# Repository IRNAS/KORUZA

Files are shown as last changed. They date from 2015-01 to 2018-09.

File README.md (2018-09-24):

Wireless optical system KORUZA
======

In this repository you can find documentation with all the plans for mechanical and electronic KORUZA parts.

Check  repository [koruza-instructions](https://github.com/IRNAS/KORUZA-instructions) if you are looking for documentation on how to assemble and use Koruza system. See [project website](http://koruza.net/) for complete specification and introduction.

Should you need any support with KORUZA system, get in touch with Institute IRNAS team. Please note that this version of the system is no longer actively supported.

---

## Licensing

We strive to make KORUZA as usefully open-source as possible.
Hardware including documentation is licensed under [CERN OHL v.1.2. license](http://www.ohwr.org/licenses/cern-ohl/v1.2)

Firmware and software originating from the project is licensed under [GNU GENERAL PUBLIC LICENSE v3](http://www.gnu.org/licenses/gpl-3.0.en.html).

Open data generated by our projects is licensed under [CC0](https://creativecommons.org/publicdomain/zero/1.0/legalcode).

All our websites and additional documentation are licensed under [Creative Commons Attribution-ShareAlike 4 .0 Unported License] (https://creativecommons.org/licenses/by-sa/4.0/legalcode).

What this means is that you can use hardware, firmware, software and documentation without paying a royalty and knowing that you'll be able to use your version forever. You are also free to make changes but if you share these changes then you have to do so on the same conditions that you enjoy.

Koruza, GoodEnoughCNC and IRNAS are all names and marks of Institut IRNAS Rače. 
You may use these names and terms only to attribute the appropriate entity as required by the Open Licences referred to above. You may not use them in any other way and in particular you may not use them to imply endorsement or authorization of any hardware that you design, make or sell.

### Contributing
By contributing to KORUZA repository you agree with the specified license and terms of use. Note significant changes in CHANGE.txt, using github comments for commits and smaller changes. 

### Manufacturing
You are required to distribute the license along with the documentation or modified documentation along with every manufactured unit. We ask you to report at monthly intervals in writing about the units you have manufactured as specified in PRODUCT.txt .

## Copyright

Copyright Institute IRNAS Rače 2016. 

This documentation describes Open Hardware and is licensed under the CERN OHL v. 1.2.
You may redistribute and modify this documentation under the terms of the [CERN OHL v.1.2.](http://ohwr.org/cernohl). This documentation is distributed WITHOUT ANY EXPRESS OR IMPLIED  WARRANTY, INCLUDING OF MERCHANTABILITY, SATISFACTORY QUALITY AND FITNESS FOR A PARTICULAR PURPOSE. Please see the CERN  OHL  v.1.2 for applicable conditions.

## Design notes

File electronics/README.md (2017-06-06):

# KORUZA control electronics

KORUZA wireless optical system is controlled through a network interface. It is based on Raspberry Pi 2B microcomputer expanded with circuit boards designed for this purpose.

The boards have been designed in Altium Designer, all sources and gerber files are available.

## KORUZA RPi shield
This board attaches directly onto the Raspberry Pi and is the input/output interface to control motors, sensors and SFP modules.

## KORUZA power module
This board accepts DC power in 12-30V (24V optimal) range and creates two regulated outputs at 5V and 9V, used for powering the Raspberry Pi and motors respectively. It attaches directly to the RPi shield or can be connected with a flat cable.

## KORUZA SFP extension plug
This board is a fake SFP module that can be plugged in an media converted and bring out the data signals. They are connected to a SATA connector as it is a high-speed differential cable commonly available.

## KORUZA SFP extension socket
This board accepts an SFP module and connects to the plug with SATA and IDC cables and to the RPi shield with an IDC cable, allowing for the remote monitoring of SFP module digital monitoring features.

# Ordering
You can order the PCBs from DirtyPCB service by following the two links or pre-panelized designs. To build KORUZA units you need two PCB panels of different thicknesses, [panel 1.0mm](http://dirtypcbs.com/view.php?share=15209&accesskey=d26ee0985b1c8a857d2a581abbbace13) and [panel 1.6mm](http://dirtypcbs.com/view.php?share=15210&accesskey=55f58673fd12db957a8ae663c1b3f456) you can order from the links provided.

---

The documentation for universal controller for unipolar stepper motors with encoders and end switches is in the repository [UniversalUnipolarStepperController](https://github.com/IRNAS/UniversalUnipolarStepperController).

Check  repository [koruza-instructions](https://github.com/IRNAS/KORUZA-instructions) if you are looking for documentation on how to assemble and use Koruza system. See [project website](http://koruza.net/) for complete specification and introduction.

Should you need any support with KORUZA system, get in touch with Institute IRNAS team and others involved in the project via [chat](https://chat.irnas.eu/).

---

#### License

All our projects are as usefully open-source as possible.

Hardware including documentation is licensed under [CERN OHL v.1.2. license](http://www.ohwr.org/licenses/cern-ohl/v1.2)

Firmware and software originating from the project is licensed under [GNU GENERAL PUBLIC LICENSE v3](http://www.gnu.org/licenses/gpl-3.0.en.html).

Open data generated by our projects is licensed under [CC0](https://creativecommons.org/publicdomain/zero/1.0/legalcode).

All our websites and additional documentation are licensed under [Creative Commons Attribution-ShareAlike 4 .0 Unported License] (https://creativecommons.org/licenses/by-sa/4.0/legalcode).

What this means is that you can use hardware, firmware, software and documentation without paying a royalty and knowing that you'll be able to use your version forever. You are also free to make changes but if you share these changes then you have to do so on the same conditions that you enjoy.

Koruza, GoodEnoughCNC and IRNAS are all names and marks of Institut IRNAS Rače. 
You may use these names and terms only to attribute the appropriate entity as required by the Open Licences referred to above. You may not use them in any other way and in particular you may not use them to imply endorsement or authorization of any hardware that you design, make or sell.

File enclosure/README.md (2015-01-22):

KORUZA enclosure
======================
The outer KORUZA enclosure houses the main 3D printed assembly and protects the device from weather as well as interfaces the mounting mechanism.

### Design overview
The enclosure is designed to be made from standard square aluminium tubing with 100mm x 100mm x 2mm dimension (outer dimensions and wall thickness) that is available from a range of suppliers. The front section features an overhang to protect the lens from direct exposure to snow and rain. 4 mounting holes on the front side on two sides serve as mounting points for the internal assembly, 4 holes on the top towards the rear for the mounting mechanism and two holes on the rear for mounting the back cover. The large hole on the bottom side is for mounting the PG16 euroflex tube connector.

### Manufacturing
The enclosure can be manufactured with the following methods:
* 3 axis CNC: Manually rotate the tube and cute each side separately. Suitable for low volume
* 4 axis CNC: Automatically cut the tube on all sides. Suitable for low volume.
* Tube laser cutter: Automatically cut all sides. Suitable for high volumes.

KORUZA enclosure

### Lid / cover
The back cover for the enclosure is 3D printed and made to house electonics. Designed in OpenSCAD and using [IRNAS OpenSCAD-Lib](https://github.com/IRNAS/OpenSCAD-lib) for common mechanical elements. 3D print from ABS, attach to enclosure with M3 screws.

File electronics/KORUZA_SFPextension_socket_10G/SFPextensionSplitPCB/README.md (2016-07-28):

# SFP extension Split

### ISSUE
* add via tenting on output (gerber) files - DONE

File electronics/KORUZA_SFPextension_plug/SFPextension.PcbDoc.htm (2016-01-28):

Reporting Options

# File in Previous Format

Date | : | 2/10/2014
Time | : | 2:40:51 PM
Filename | : | Z:\Projects\AltiumProjects\SFPextension.PcbDoc

Version | Warning
Altium Designer update 19 | CAUTION - Air Gap Width attribute was introduced to Polygon Connect Style Rule. Air Gap Width attribute now controls the distance between poured polygon and pads on the same net - this value was previosuly taken from clearance rule while ignoring net subscope leading to sometime unexpected results.
Release 13 | CAUTION - Silkscreen Over Component Pads Rules are converted to Silk To Solder Mask Clearance Rules. Suggest examining rule scopes for accuracy.
Release 14 | CAUTION - The Differential Pairs Routing rule added support for control of the width. Be aware that Width rules pertaining to differential pairs need to be manually moved to the Differential Pairs Routing rule.

This file was generated by an earlier version of the software

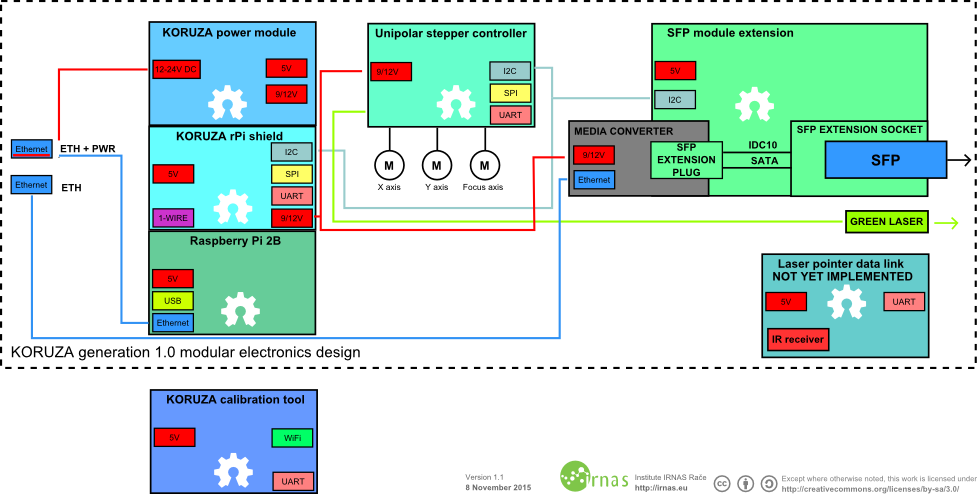
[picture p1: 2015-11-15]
diagrams/ElectronicsDiagram.png

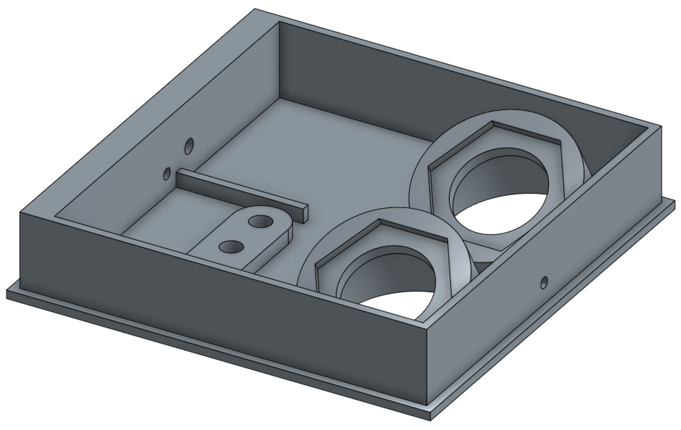
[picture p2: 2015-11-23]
enclosure/enclosure_cover.png

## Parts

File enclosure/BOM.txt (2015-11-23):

1 enota:

1x square tube 100x100x2 x 475mm
1x L profile 100x100x5 x 250mm
1x U profile 100x35x5 x 160mm
1x pritrditev za na štango z vsemi vijaki

1x bolt_eye_DIN444A_M10x45
2x nut_thin_ISO4035_M10

1x bolt_round_head_square_neck_DIN603_M10x70
1x washer_spring_lock_DIN127_M10
3x nut_thin_ISO4035_M10

1x bolt_HEX_ISO4017_DIN933_M10x160
1x washer_spring_lock_DIN127_M10
7x nut_thin_ISO4035_M10

2x screw_M4
2x washer_spring_lock_DIN127_M4
2x nut_DIN934_M4

+ spring washer m10 in m4
+ šrauf m4
+ assembly

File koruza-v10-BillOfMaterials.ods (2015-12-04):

KORUZA generation 1.0 – Bill of materials
Institute IRNAS Rače – Licensed under CERN OHL – 2.12.2015
Preliminary information, not for ordering or general use, you have been warned!
Module | Sub-module | Part name | Description | Quantity | Part nr.
Electronics |  | Power module | Circuit board from 24V in to 5V and 9V out | 1 | E-1
Electronics |  | Raspberry pi shield | Shield for interfacing Rpi with KORUZA electronics | 1 | E-2
Electronics |  | Sfp extension plug | Module for interfacing Media converter | 1 | E-3
Electronics |  | Sfp extension socket | Module for interfacing SFP module | 1 | E-4
Electronics |  | Universal unipolar stepper driver | Module for controlling stepper motors and green laser | 1 | E-5
Electronics |  | Raspberry Pi 2B microcomputer | Brains of the system | 1 | E-6
Electronics |  | PoE injector 24V | Passive PoE injector | 1 | E-7
Electronics |  | SFP module 40km+ BiDi SC with DDM | Electro-optical transceiver | 1 | E-8
Electronics |  | Green laser 5mV, 3.3V |  | 1 | E-9
Electronics |  | Motor 24BYJ48 |  | 3 | E-10
Electronics |  | Waterproof eth connector |  | 1 | E-11
Electronics |  | Waterproof eth + pwr connectors |  | 1 | E-12
Electronics |  | TP-Link MC220L media converter |  | 1 | E-13
Electronics |  | Cable IDC long | IDC10 35cm | 1 | E-14
Electronics |  | Cable IDC short | IDC10 10cm | 1 | E-15
Electronics |  | SATA cable | 10cm long, straight straing | 1 | E-16
Electronics |  | Micromatch cable | 25cm | 1 | E-17
Electronics |  | Cable power 0.75mm^2 red-black | 20cm | 1 | E-18
Electronics |  | Cable power jack 2.1mm | 25cm | 1 | E-19
Electronics |  | Micro SD card, 8GB |  | 1 | E-20
Mechanical | Fasteners | Set screw HEX socket DIN913 M3x16 |  | 1 | M-F1
Mechanical | Fasteners | Screw HEX socket DIN912 M3x25 |  | 9 | M-F3
Mechanical | Fasteners | Screw HEX socket DIN912 M3x35 |  | 18 | M-F4
Mechanical | Fasteners | Screw HEX socket DIN912 M4x45 |  | 4 | M-F5
Mechanical | Fasteners | Screw TORX BN6404 M3x10 |  | 17 | M-F6
Mechanical | Fasteners | Screw HEX socket DIN912 M4x12 |  | 12 | M-F7
Mechanical | Fasteners | Screw HEX socket DIN912 M4x70 |  | 2 | M-F8
Mechanical | Fasteners | Screw HEX DIN933 M5x80 | 70mm to 80mm length works equally well | 1 | M-F9
Mechanical | Fasteners | Threaded rod M5x65 |  | 2 | M-F10
Mechanical | Fasteners | Nut, square DIN562 M3 |  | 42 | M-F11
Mechanical | Fasteners | Nut, square DIN562 M4 |  | 22 | M-F12
Mechanical | Fasteners | Long nut, HEX DIN6334 M5 |  | 3 | M-F13
Mechanical | Fasteners | Washer M3 DIN921 |  | 3 | M-F14
Mechanical | Fasteners | Washer M4 DIN921 |  | 7 | M-F15
Mechanical | Fasteners | Thin nut ISO4035 M10 |  | 10 | M-F16
Mechanical | Fasteners | Eye bolt Screw DIN444A M10x40 |  | 1 | M-F17
Mechanical | Fasteners | Screw round head square neck bolt DIN603 M10x75 |  | 1 | M-F18
Mechanical | Fasteners | Screw HEX bolt DIN933 M10x160 |  | 1 | M-F19
Mechanical | Fasteners | Washer M10 |  | 4 | M-F20
Mechanical | Fasteners | Spring lock washer DIN127 M10 |  | 3 | M-F21
Mechanical | Fasteners | Nut, HEX, M5 DIN934 M5 |  | 1 | M-F22
Mechanical | 3D Printed | SFP module sleeve |  | 1 | M-P1
Mechanical | 3D Printed | SFP mount |  | 1 | M-P2
Mechanical | 3D Printed | Ring outer |  | 1 | M-P4
Mechanical | 3D Printed | Ring inner |  | 1 | M-P5
Mechanical | 3D Printed | Lens mount outer |  | 1 | M-P6
Mechanical | 3D Printed | Lens mount |  | 1 | M-P7
Mechanical | 3D Printed | Laser mount |  | 1 | M-P8
Mechanical | 3D Printed | Wedge left |  | 1 | M-P9
Mechanical | 3D Printed | Wedge right |  | 1 | M-P10
Mechanical | 3D Printed | MC mount |  | 1 | M-P12
Mechanical | 3D Printed | Motor mount |  | 1 | M-P13
Mechanical | 3D Printed | Inner SFP mount |  | 1 | M-P14
Mechanical | 3D Printed | Lid |  | 1 | M-P15
Mechanical | 3D Printed | bracket |  | 4 | M-P16
Mechanical | 3D Printed | Half-bracket |  | 1 | M-P17
Mechanical | 3D Printed | Pin with hole |  | 2 | M-P18
Mechanical | 3D Printed | Triangle |  | 1 | M-P19
Mechanical | Other | Rubber | 10x10cm 5mm not reinforced | 1 | M-O1
Mechanical | Other | 8mm stainless steel rod – 200mm |  | 4 | M-O2
Mechanical | Other | Lens | Plano convex 50mm FL=100mm | 1 | M-O3
Mechanical | Other | Spring 10x20x0.7mm |  | 2 | M-O4
Mechanical | Other | Sliding bushing |  | 6 | M-O6
Mechanical | Other | Cable ties 200x3.6mm |  | 2 | M-O7
Mechanical | Other | Coupler M5 |  | 3 | M-O8
Mechanical | Other | M3 male-female spacer 10mm long |  | 10 | M-O9
Mechanical | Other | Spring 49/35/4 |  | 1 | M-O10
Mechanical | Other | Bearing F624ZZ |  | 1 | M-O11
Mechanical | Other | Square profile | Custom made | 1 | M-E1
Mechanical | Enclosure | U-profile | Custom made | 1 | M-E2
Mechanical | Enclosure | L-profile | Custom made | 1 | M-E3
Mechanical | Enclosure | Mounting bracket set |  | 1 | M-E4
Tools |  | Philips screwdriver
Tools |  | Hammer
Tools |  | Combination pliers
Tools |  | tongue-and-groove pliers
Tools |  | slotted screwdriver
Tools |  | HEX key 1.5, 2.5, 3mm
Tools |  | utility knife
Tools |  | Battery drill
Tools |  | drill 3mm, 8mm, 8.1mm
Tools |  | 10mm reamer
Tools |  | TORX screwdriver T10
Tools |  | measuring tape

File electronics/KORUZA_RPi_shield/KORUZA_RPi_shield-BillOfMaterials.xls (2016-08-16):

KORUZA Raspberry PI shield Bill of Materials
Comment | Description | Designator | Footprint | LibRef | Quantity | Order | Farnell | TME
Capacitor | Capacitor MLLC 100n 5V | C1, C3, C4, C6, C7, C9 | 0603 | Capacitor | 6 |  | http://si.farnell.com/tdk/c1608x5r1h104k080aa/cap-mlcc-x5r-100nf-50v-0603/dp/2211177
Capacitor | Capacitor, Tantalum, 10uF 10% 20V MCCT-B (3528) | C2, C5, C8 | AVX-CAPC3528_V | CMP-0279-00001-1 | 3 |  | http://si.farnell.com/avx/taja106m016r/cap-tant-10uf-16v-case-a/dp/2333010
DC power connection | Screw terminal block, 2way | Conn1, Conn2, Conn3 | MKDSN 2,5/ 2-5,08 and powercon | PowerScrewTerminal | 3 |  | http://si.farnell.com/camdenboss/ctb0102-2/terminal-block-wire-to-brd-2pos/dp/2493614
LED | LED diode smd right angle white | D1, D2, D3 | 1206/0805 diode | LED | 3 |  | http://si.farnell.com/multicomp/ovs-2101/led-2-8x0-8x1-2mm-side-emitting/dp/1716775
Zener | Zener diode 15V | D4 | DIOMELF3517N | Zener | 1 |  | http://si.farnell.com/vishay-semiconductor/zmy15-gs08/diode-zener-1w-15v/dp/1617743
1A | 1A fuse PTC SMD | F1 | 1210 | Fuse | 1 |  | http://si.farnell.com/multicomp/mc36221/fuse-ptc-reset-smd-6v-1a/dp/1861192
IDC10 | IDC 10 pin male | P1, P6, P8 | IDC10 | IDC10 | 3 |  | http://si.farnell.com/amphenol/t821110a1s100ceu/header-vertical-2-54mm-10way/dp/2215304
Header for RaspberryPI | Header, 40-pin, 2 row, 2.54mm pitch | P2 | RaspberryPI_B+ | RaspberryPI 2B | 1 |  | http://si.farnell.com/harwin/m20-6112045/socket-pc-104-40way/dp/1569232
Header 3 | Header, 3-Pin | P3, P4 | HDR1X3 | Header 3 | 2 | one header 40pin breakable needed | http://si.farnell.com/te-connectivity-amp/825433-5/header-1row-5way/dp/1187826
Header 2 | Header, 2-Pin | P5, P9 | HDR1X2 | Header 2 | 2 | one header 40pin breakable needed | http://si.farnell.com/te-connectivity-amp/825433-5/header-1row-5way/dp/1187826
Header 5 | Header, 5-Pin | P7 | HDR1X5 | Header 5 | 1 | one header 40pin breakable needed | http://si.farnell.com/te-connectivity-amp/825433-5/header-1row-5way/dp/1187826
Micromatch | Micro-Match female PCB connector 10 Positions THT | PoExtension1, PoExtension2 | 8-188275-0 | 1-215079-0 | 2 |  | http://si.farnell.com/te-connectivity-amp/8-188275-0/connector-receptacle-smt-1-27mm/dp/3784745
Resistor 10k | Resistor 0805 smd | R1, R5, R7, R8, R9, R10, R11, R12, R13, R14, R19, R21, R22, R23, R25 | RESC2012X06N | Resistor | 15 |  | http://si.farnell.com/multicomp/mc0063w0603510k/res-thick-film-10k-5-0-063w-0603/dp/9331700
Resistor 0 | Resistor 0805 smd | R2, R4, R18, R20, R24 | RESC2012X06N | Resistor | 5 |  | http://si.farnell.com/multicomp/mc0063w06030r/resistor-thick-film-0r-0-063w/dp/9331662
Resistor 4k7 | Resistor 0805 smd | R3, R6 | RESC2012X06N | Resistor | 2 |  | http://si.farnell.com/multicomp/mc0063w060354k7/res-thick-film-4k7-5-0-063w-0603/dp/9332154
Resistor 1k | Resistor 0805 smd | R15, R16, R17 | RESC2012X06N | Resistor | 3 |  | http://si.farnell.com/multicomp/mc0063w060354k7/res-thick-film-4k7-5-0-063w-0603/dp/9332154
Mosfet NDT2955 | P MOSFET | T1, T2, T3 | SOT230P700X180-4N | NDT2955 | 3 |  | http://si.farnell.com/fairchild-semiconductor/ndt2955/mosfet-p-ch-60v-2-5a-sot-223/dp/9846271
Voltage regulator | LD1117S33TR | U1, U2, U3 | SOT-223_L | CMP-0244-00310-1 | 3 |  | http://si.farnell.com/texas-instruments/lm1117mp-3-3/v-reg-ldo-3-3v-1117-sot-223-3/dp/9778195
Transistor array | Darlington array ULN2003 | U4 | SO-16 narrow | ULN2003 | 1 |  | http://si.farnell.com/texas-instruments/uln2003adr/darlington-array-7npn-2003ade4/dp/1125398RL

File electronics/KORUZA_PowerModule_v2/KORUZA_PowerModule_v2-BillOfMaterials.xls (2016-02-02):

KORUZA Power module V2
Comment | Description | Designator | Footprint | LibRef | Quantity | Order | Farnell | TME
Power innput | Screw terminal or DC socket | Conn1 | MKDSN 2,5/ 2-5,08 | PowerScrewTerminal | 1 |  | http://si.farnell.com/multicomp/mj-180ph/socket-pcb-dc-power-12vdc-4a/dp/1737251
9V output | Screw terminal | Conn2 | MKDSN 2,5/ 2-5,08 | PowerScrewTerminal | 1 |  | http://si.farnell.com/camdenboss/ctb0102-2/terminal-block-wire-to-brd-2pos/dp/2493614
LED | LED diode | D1 | 1206/0805 diode | LED | 1 |  | http://si.farnell.com/rohm/sml-310vtt86l/led-smd-0603-red/dp/1685064
TVS diode | TVS bidirectional diode 36V | D2 | DIOM4750X18N | TVS diode | 1 |  | http://si.farnell.com/vishay-semiconductor/smaj36ca-e3-61/diode-tvs-400w-36v-bidir-sma/dp/1698863RL
IDC10 | IDC 10pin male | P1 | IDC10 | IDC10 | 0 | if using cable | http://si.farnell.com/amphenol/t821110a1s100ceu/header-vertical-2-54mm-10way/dp/2215304
IDC10 | IDC 10pin female | P1 | IDC10 | IDC10 | 1 | if connected to shield | http://si.farnell.com/multicomp/2214s-10sg-85/socket-pcb-2-row-vert-10way/dp/1593490
Header 2 | Header, 2-Pin | P2, P4 | HDR1X2 | Header 2 | 1 | do not install
USB | USB A standard receptacle | P3 | USB A THT | USB | 1 | do not install
1k | Resistor 0805 smd | R1 | RESC2012X06N | Resistor | 1 | do not install
LM2596 module | LM2596 module | U1, U2 | LM2596 module | LM2596 module | 2 | do not install

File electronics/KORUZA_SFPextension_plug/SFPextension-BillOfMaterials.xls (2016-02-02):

KORUZA SFP extension plug
Comment | Description | Designator | Footprint | LibRef | Quantity | Order | Farnell | TME
SATA | sata | P1 | SATA pcb | SATA | 1 |  | http://si.farnell.com/webapp/wcs/stores/servlet/ProductDisplay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
IDC10 | Header, 5-Pin, Dual row | P4 | HDR2X5_CEN | Header 5X2A | 1 |  | http://si.farnell.com/amphenol/t821110a1s100ceu/header-vertical-2-54mm-10way/dp/2215304
SFP connector |  | SFP1 | SFP pcb con | SFP connector | 0 | PCB itself

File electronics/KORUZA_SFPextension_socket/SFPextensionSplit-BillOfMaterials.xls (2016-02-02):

KORUZA SFP extension socket
Comment | Description | Designator | Footprint | LibRef | Quantity | Order | Farnell | TME
Capacitor | General capacitor | C1 | RESC2012X06N | Capacitor | 1
SATA | sata | P1 | SATA pcb | SATA | 1 |  | http://si.farnell.com/webapp/wcs/stores/servlet/ProductDisplay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
IDC10 | IDC 10pin | P2, P3 | IDC10 | IDC10 | 2 |  | http://si.farnell.com/amphenol/t821110a1s100ceu/header-vertical-2-54mm-10way/dp/2215304
SFP connector |  | SFP1 | SFP receptacle | SFP connector | 1 |  | http://si.farnell.com/te-connectivity/1888247-2/connector-sfp-rcpt-20pos-smt/dp/2399618
SFP cage |  | SFP1 | SFP cage | SFP cage | 1 |  | http://si.farnell.com/amphenol-commercial-products/u77a1118200t/cage-1-port-sfp-connector/dp/1256177

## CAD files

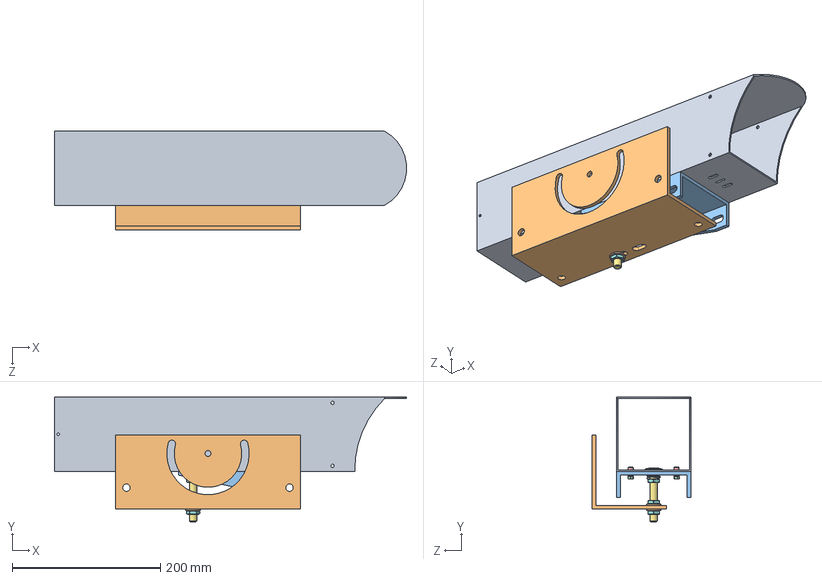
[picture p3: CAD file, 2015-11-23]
enclosure/enclosure.SLDASM
474.7 x 168.0 x 133.0 mm
square tube 100x100x2
L profile 100x100x5
U profile 100x35x5
nut_DIN934_M4 x 2
screw_HEX_SOCKET_ISO4762_DIN912_M4x12 x 2
washer_spring_lock_DIN127_M4 x 2
bolt_round_head_square_neck_DIN603_M10x70
nut_thin_ISO4035_M10 x 3
washer_spring_lock_DIN127_M10
washer_ISO7089_DIN125A_M10_10.5x20 x 2

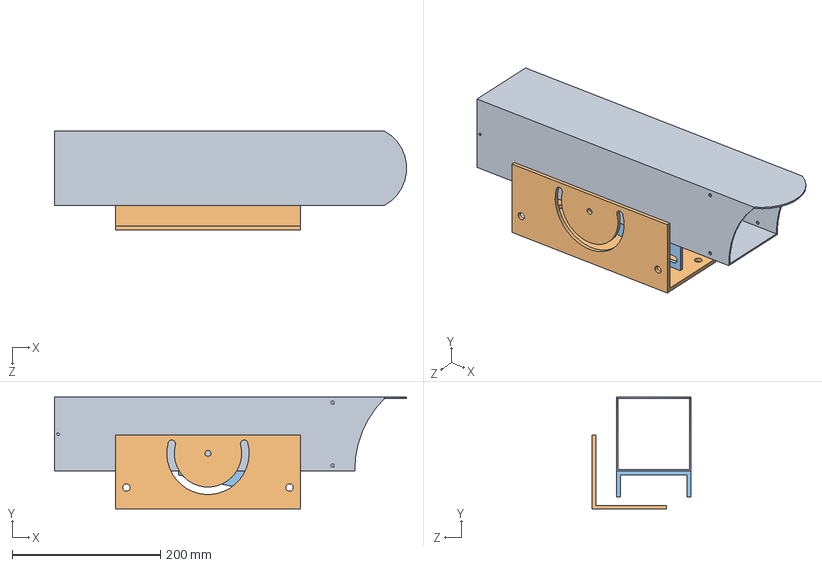
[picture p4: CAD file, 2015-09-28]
enclosure/koruza enclosure.SLDASM
474.7 x 151.0 x 133.0 mm
square tube 100x100x2
L profile 100x100x5
U profile 100x35x5

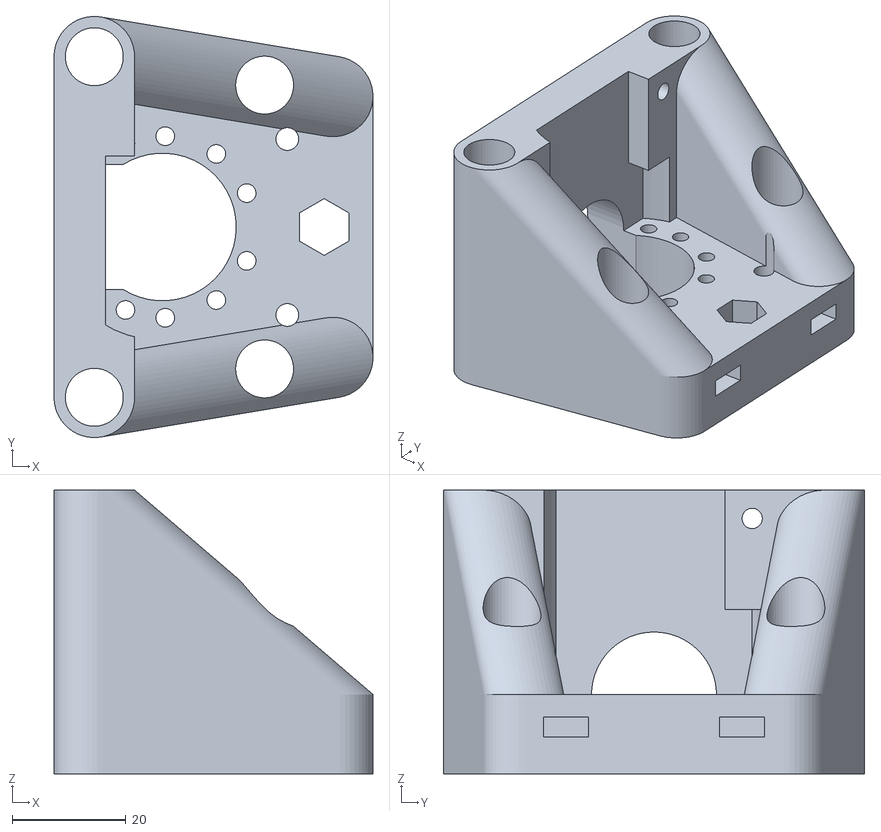
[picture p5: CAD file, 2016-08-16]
main_structure/koruza-v10-10G-sfp_mount.stl
56.2 x 74.2 x 50.0

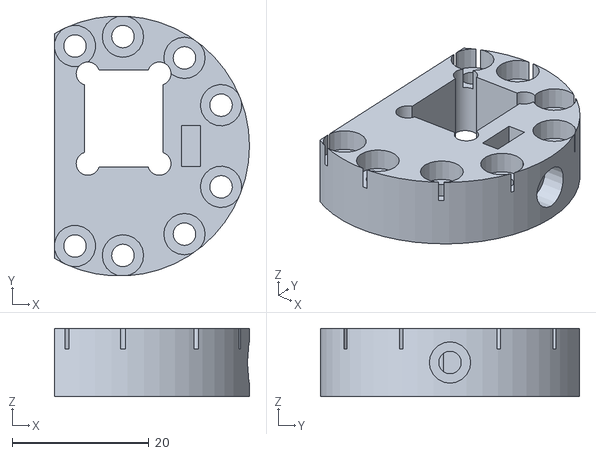
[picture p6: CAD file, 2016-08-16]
main_structure/koruza-v10-10G-sfp_mount_bracket.stl
28.5 x 37.9 x 10.0

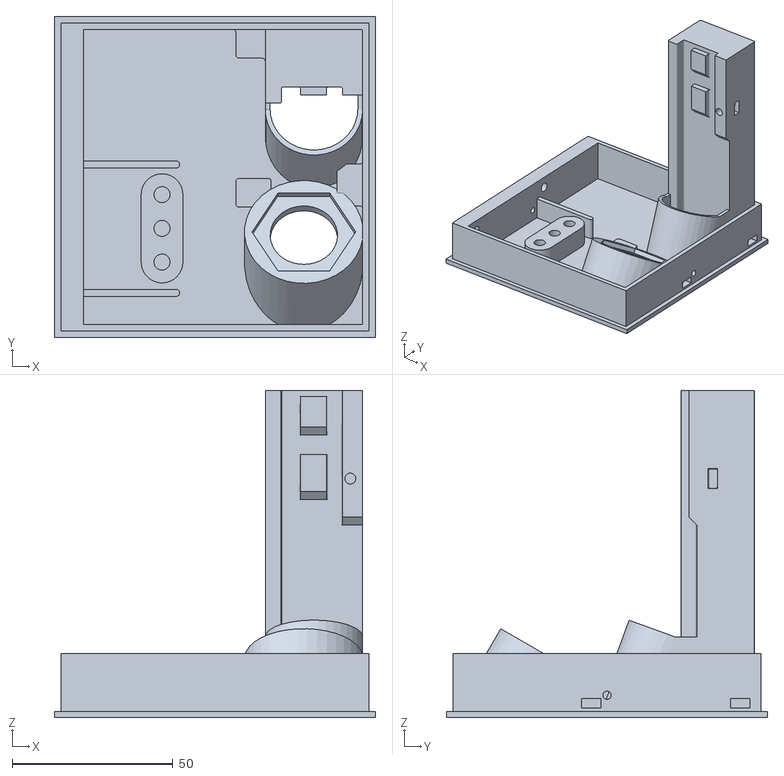
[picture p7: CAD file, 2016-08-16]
main_structure/koruza-v10-10G-enclosure-cover.stl
100.0 x 100.0 x 102.0

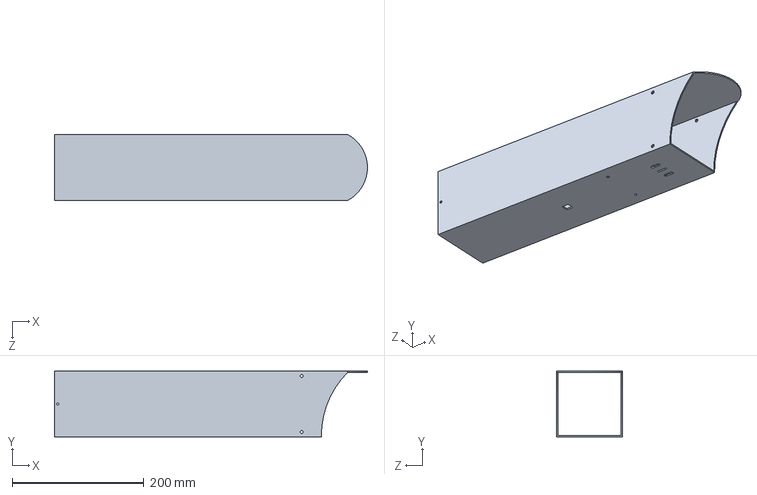
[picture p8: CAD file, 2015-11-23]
enclosure/square tube 100x100x2.STEP
475.0 x 100.0 x 100.0 mm

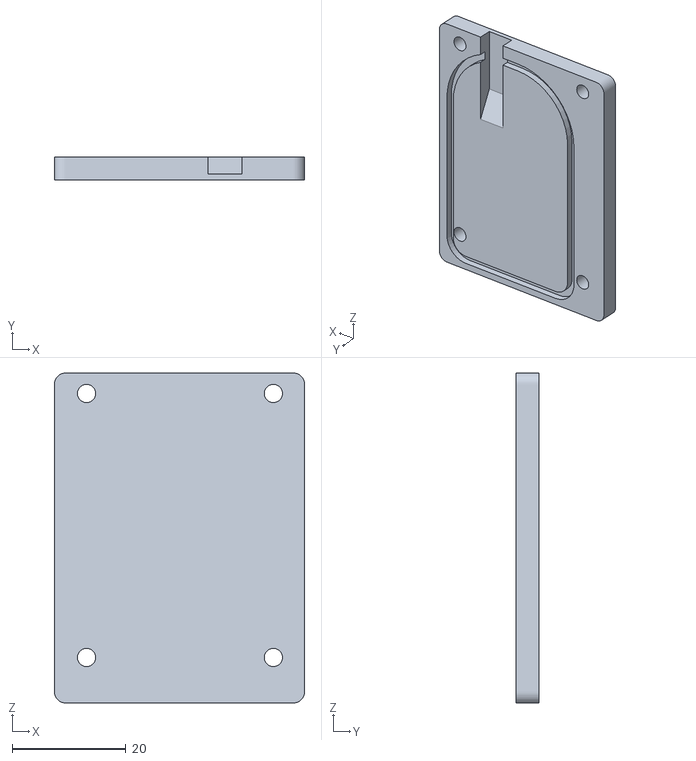
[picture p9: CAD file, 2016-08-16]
main_structure/koruza-v10-10G-enclosure-cover-lid.stl
44.0 x 4.00 x 58.0

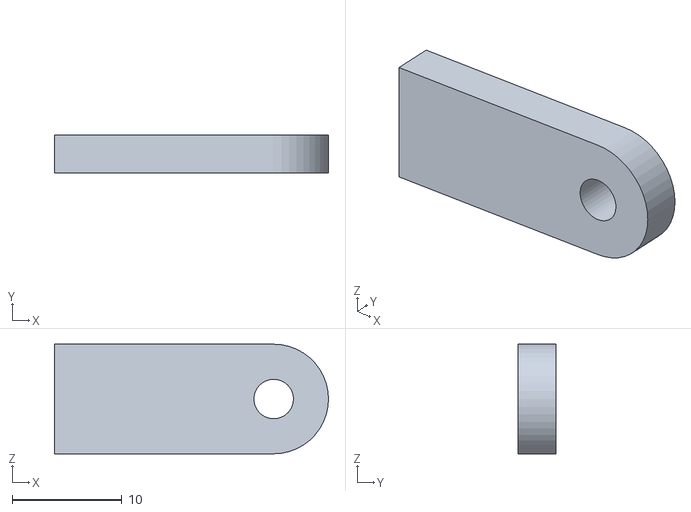
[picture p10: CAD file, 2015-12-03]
main_structure/koruza-v10-halfbracket.stl
25.0 x 3.50 x 10.0

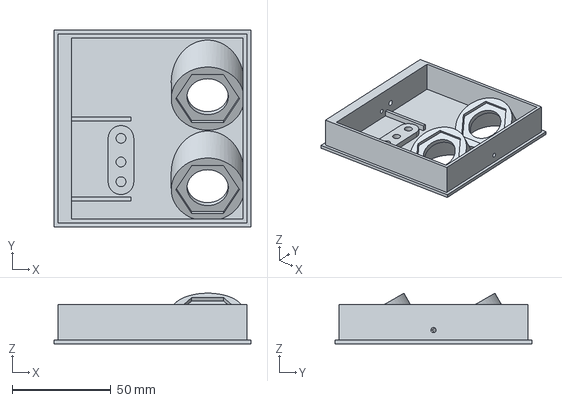
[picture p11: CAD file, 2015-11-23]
enclosure/enclosure_cover.step
100.0 x 100.0 x 25.7 mm

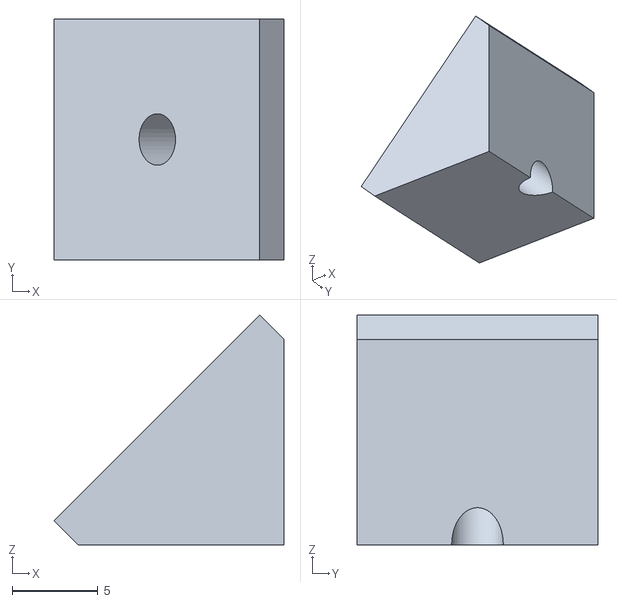
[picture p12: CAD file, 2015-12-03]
main_structure/koruza-v10-triangle.stl
13.4 x 14.0 x 13.4

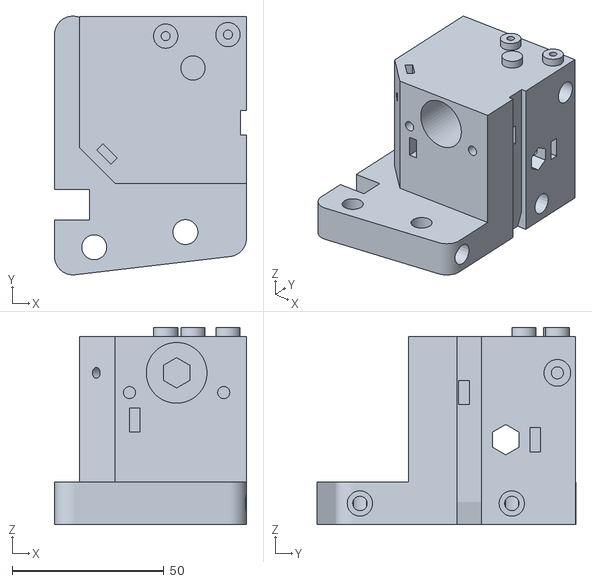
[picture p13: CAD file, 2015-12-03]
main_structure/koruza-v10-motor_mount.stl
63.2 x 85.2 x 65.0

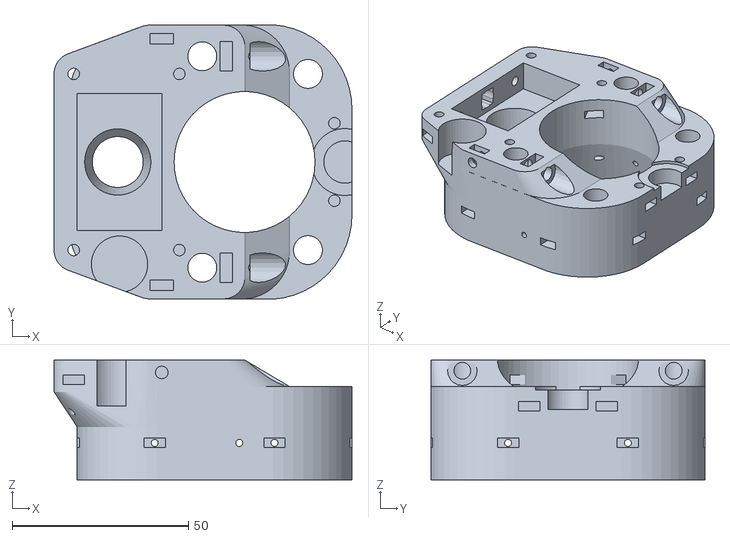
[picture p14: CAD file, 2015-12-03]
main_structure/koruza-v10-laser_mount.stl
84.6 x 77.9 x 34.0

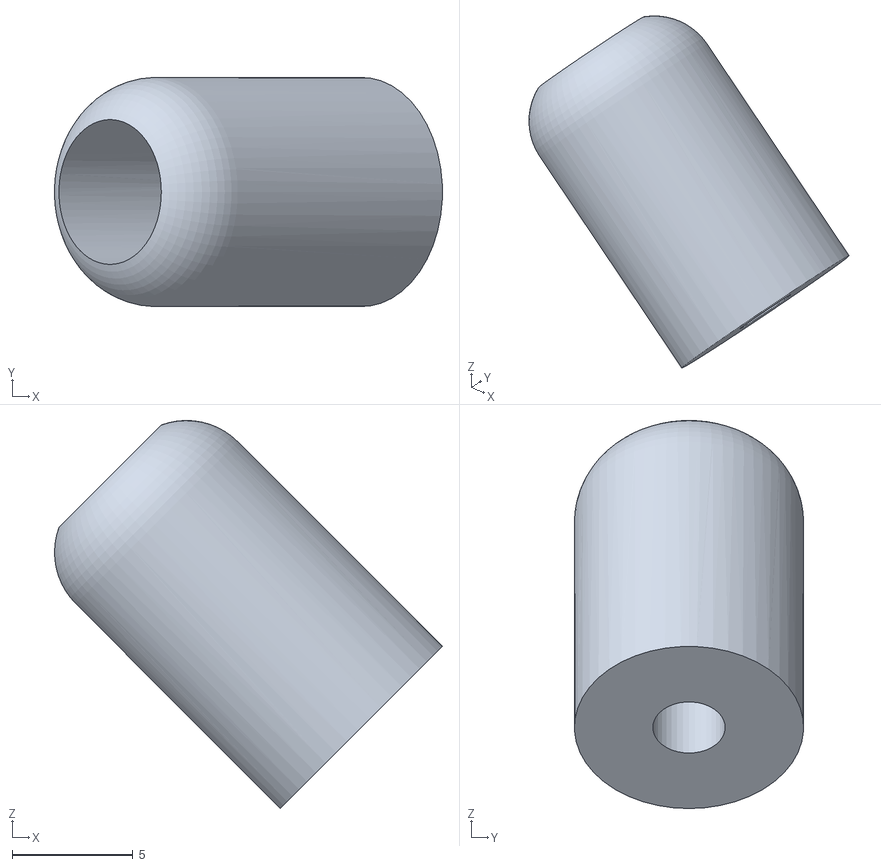
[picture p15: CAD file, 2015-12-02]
main_structure/koruza-v10-pin-hole.stl
16.1 x 9.50 x 16.1

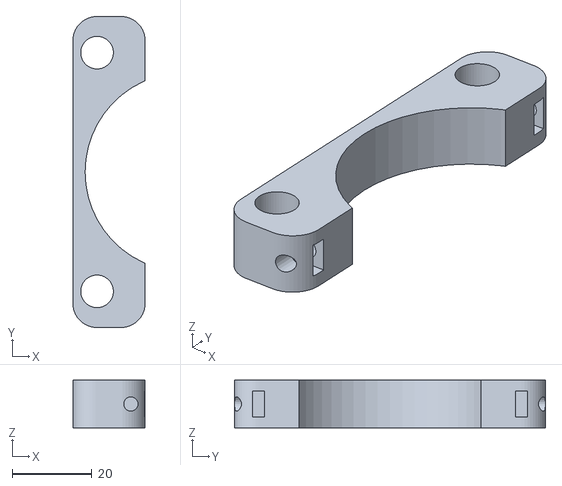
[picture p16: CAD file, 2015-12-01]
main_structure/koruza-v10-mc_mount.stl
18.2 x 78.2 x 12.0

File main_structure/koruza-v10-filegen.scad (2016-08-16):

use <koruza-v10.scad>

//parts for KORUZA in printing configuration

// Combined print - Outer ring and lens lid

// rotate(a=[0,180,0]) rotate(a=[-2,2,0]) part_mounting_ring_outer();
// rotate(a=[0,180,0]) translate([0,0,0])  part_lens_mount_outer();

mode=12;

if (mode == 0) {
    //openscad -Dmode=0 -o koruza-v10-comb-ring_outer-lens_outer.stl koruza-v10-filegen.scad
    rotate(a=[0,0,0]) rotate(a=[2,-2,0]) part_mounting_ring_outer();
    rotate(a=[0,0,0]) translate([0,0,-2])  part_lens_mount_outer();
} else if (mode == 1) {
     //openscad -Dmode=1 -o koruza-v10-comb-ring_inner-lens_mount.stl koruza-v10-filegen.scad
    rotate(a=[2,-2,0]) part_mounting_ring_inner();
    translate([0,0,0])  part_lens_mount();
} else if (mode == 2) {
     //openscad -Dmode=2 -o koruza-v10-laser_mount.stl koruza-v10-filegen.scad
     translate([0,0,-3.5])  part_laser_mount();
} else if (mode == 3) {
     //openscad -Dmode=3 -o koruza-v10-laser_wedges.stl koruza-v10-filegen.scad
     rotate(a=[180,0,0]){translate([0,5,0]) part_laser_adj_l();part_laser_adj_r();}
} else if (mode == 4) {
     //openscad -Dmode=4 -o koruza-v10-sfp_mount.stl koruza-v10-filegen.scad
     part_sfp_mount();
} else if (mode == 5) {
     //part not required anymore
     //openscad -Dmode=5 -o koruza-v10-sfp_spring_mount.stl koruza-v10-filegen.scad
     //part_sfp_spring_mount();
} else if (mode == 6) {
     //openscad -Dmode=6 -o koruza-v10-motor_mount.stl koruza-v10-filegen.scad
     part_motor_mount();    
} else if (mode == 7) {
     //openscad -Dmode=7 -o koruza-v10-mc_mount.stl koruza-v10-filegen.scad
     translate([0,0,-127]) part_mc_mount(); 
} else if (mode == 8) {
     //openscad -Dmode=8 -o koruza-v10-mc_plate.stl koruza-v10-filegen.scad
     rotate(a=[90,0,0]) part_mc_plate();
    translate([0,13,0])
    rotate(a=[90,0,0]) part_mc_plate();
    translate([0,13*2,0])
    rotate(a=[90,0,0]) part_mc_plate();
    translate([0,13*3,0])
    rotate(a=[90,0,0]) part_mc_plate();     
} else if (mode == 9) {
     //openscad -Dmode=9 -o koruza-v10-sfp_mount_bracket.stl koruza-v10-filegen.scad
    sfp_mount_bracket(); 
}
else if (mode == 10) {
     //openscad -Dmode=10 -o koruza-v10-rpi_plate.stl koruza-v10-filegen.scad
    part_rpi_plate(); 
}else if (mode == 11) {
     //openscad -Dmode=11 -o koruza-v10-sfp_mount_LC.stl koruza-v10-filegen.scad
     part_sfp_mount_lc();
}else if (mode == 12) {
     //openscad -Dmode=12 -o koruza-v10-sfp_mount_bracket_LC.stl koruza-v10-filegen.scad
     sfp_mount_bracket_lc(); 
}












////////// parts for mounting to enclosure

// rotate(a=[-2,-2,0]) part_mounting_ring_inner();
// rotate(a=[-2,-2,0]) part_mounting_ring_outer();

////////// parts for mounting the lens

// translate([0,0,-2]) part_lens_mount_outer();
// part_lens_mount();

////////// parts for mounting the aiming laser

// translate([0,0,-3.5])  part_laser_mount();
//old // part_laser_adj_mount();
// rotate(a=[180,0,0]){translate([0,5,0]) part_laser_adj_l();part_laser_adj_r();}

////////// parts for mounting the sfp module

// part_sfp_mount();
// part_sfp_spring_mount();

////////// parts for mounting the x y motors

// part_motor_mount();

////////// part rubber

//projection(cut = true) part_rubber();

////////// parts for various mounting

// translate([0,0,-127]) part_mc_mount();

/*
rotate(a=[90,0,0]) part_mc_plate();
translate([0,13,0])
rotate(a=[90,0,0]) part_mc_plate();
translate([0,13*2,0])
rotate(a=[90,0,0]) part_mc_plate();
translate([0,13*3,0])
rotate(a=[90,0,0]) part_mc_plate();
*/

////////// printing combinations


/* rotate(a=[-2,2,0]) part_mounting_ring_inner();
 translate([0,0,-3.5])  part_lens_mount(); */

/* rotate(a=[0,180,0]) rotate(a=[-2,2,0])part_mounting_ring_outer();
 rotate(a=[0,180,0]) translate([0,0,0])  part_lens_mount_outer(); */

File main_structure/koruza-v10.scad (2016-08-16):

use <24byj48.scad>
use <OpenSCAD-lib/DIN_screw_nut.scad>

res=50;

//part desing instructions
//design each part around 0,0,0 coordianates and translate it into place

///////////////////////////////////////////////////////////////////////////////
// global
// at distance 270mm from pivot we have 15mm motorized movement

offset = 8.5; //  optical axis offset from part offset

///////////////////////////////////////////////////////////////////////////////
//lens mount interfacing between laser mount and rubber
lens_mount_d_bot=74; //diameter towards bottom
lens_mount_d_top=78; //diameter towards top

lens_mount_radius=24;

//optical lens model
module hull_cube(width,rad,height){
    
    hull(){
    for (i = [[-1,-1,0],[1,-1,0],[-1,1,0],[1,1,0]]){
        translate(i*(width/2-rad)) cylinder(h=height,r=rad,center=false,$fn=res);
    }
}

	//cylinder(h=lens_thickness-1,r1=lens_mount_d_bot/2,r2=lens_mount_d_top/2,center=false,$fn=res);
}

//hull_cube(lens_mount_d_bot,lens_mount_radius,1);


///////////////////////////////////////////////////////////////////////////////
//optical lens
lens_diameter=51.2; //diameter of the lens in mm
lens_thickness=2.5; //thickness of the lens in mm
lens_bfl=100-10; //back focal lengt in mm

lens_mounting_ring_t=1; // tickness of the rign holding lens in place

//optical lens model
module lens(){
	translate([0,0,lens_mounting_ring_t])cylinder(h=lens_thickness,r=lens_diameter/2,center=false,$fn=res);
    translate([0,0,0])cylinder(h=lens_mounting_ring_t,r=lens_diameter/2-1,center=false,$fn=res);
}

//beam path from lens to receiver that must be clear for optics
module beam_path(){
	//beam path
	translate([0,0,0])
	cylinder(h=lens_bfl,r1=lens_diameter/2-lens_mounting_ring_t,r2=0,center=false,$fn=res);
}

//translate([offset,0,0]) lens();
//translate([offset,0,0]) beam_path();

//////////////////////////////////////////////////////////////////////////////

// stacking rods
rod_diameter = 8;
rod_length = 185;
rod_offset_x_t = 12;
rod_offset_y_t = 30;
rod_offset_x_b = 18;
rod_offset_y_b = 25;
rod_offset_z = -10;
rod_diameter_tolerance=0.2;


module rods(diameter,tolerance){
    for (i = [[-rod_offset_x_t,-rod_offset_y_t,0],[rod_offset_x_b,-rod_offset_y_b,0],[-rod_offset_x_t,rod_offset_y_t,0],[rod_offset_x_b,rod_offset_y_b,0]]){
        translate([offset,0,rod_offset_z]) translate(i) cylinder(h=rod_length,r=(diameter+tolerance)/2,center=false,$fn=res);
    }
}

rods(rod_diameter,rod_diameter_tolerance);

rod_plate_diameter = 18;

module rods_plate(diameter,tolerance){
    difference(){
        hull(){
            for (i = [[-rod_offset_x_t-7,-rod_offset_y_t-3,0],[rod_offset_x_b+14,-rod_offset_y_b-2,0],[-rod_offset_x_t-7,rod_offset_y_t+10,0],[rod_offset_x_b+14,rod_offset_y_b-2,0]]){
                translate([offset,0,rod_offset_z]) translate(i) cylinder(h=14,r=(diameter+4+tolerance)/2,center=false,$fn=res);
            }
        }
        rods(diameter,rod_diameter_tolerance);
    }
}

module rods_plate_sfp(diameter,tolerance){
    difference(){
        union(){
        hull(){
            for (i = [[-rod_offset_x_t,-rod_offset_y_t,0],[rod_offset_x_b+12,-rod_offset_y_b+2,0],[-rod_offset_x_t,rod_offset_y_t,0],[rod_offset_x_b+12,rod_offset_y_b-2,0]]){
                translate([offset,0,rod_offset_z]) translate(i) cylinder(h=14,r=(diameter+4+tolerance)/2,center=false,$fn=res);
            }
        }
        hull(){
            translate([offset,0,rod_offset_z]) translate([-rod_offset_x_t,-rod_offset_y_t,0]) cylinder(h=50,r=(diameter+4+tolerance)/2,center=false,$fn=res);
            translate([offset,0,rod_offset_z]) translate([rod_offset_x_b+12,-rod_offset_y_b+2,0]) cylinder(h=14,r=(diameter+4+tolerance)/2,center=false,$fn=res);
        }
        hull(){
            translate([offset,0,rod_offset_z]) translate([-rod_offset_x_t,rod_offset_y_t,0]) cylinder(h=50,r=(diameter+4+tolerance)/2,center=false,$fn=res);
            translate([offset,0,rod_offset_z]) translate([rod_offset_x_b+12,rod_offset_y_b-2,0]) cylinder(h=14,r=(diameter+4+tolerance)/2,center=false,$fn=res);
        }
        hull(){
            for (i = [[-rod_offset_x_t,rod_offset_y_t,0],[-rod_offset_x_t,-rod_offset_y_t,0]]){
                translate([offset,0,rod_offset_z]) translate(i) cylinder(h=50,r=(diameter+4+tolerance)/2,center=false,$fn=res);
            }
        }
    }
        rods(diameter,rod_diameter_tolerance);
    }
}

//translate([0,0,lens_bfl-1]) rods_plate_sfp(10,rod_diameter_tolerance);

module rods_plate_single_bot(diameter,tolerance){
    difference(){
         hull(){
        for (i = [[rod_offset_x_b,-rod_offset_y_t+2,0],[rod_offset_x_b+16,-rod_offset_y_b,0],[rod_offset_x_b,rod_offset_y_t-2,0],[rod_offset_x_b+16,rod_offset_y_b,0]]){
                translate([offset,0,0]) translate(i) cylinder(h=10,r=(diameter+4+tolerance)/2,center=false,$fn=res);
            }
        }
        rods(diameter,rod_diameter_tolerance);
        //set screws
        translate([40,-rod_offset_y_b,5]) rotate(a=[0,90,0])screw_din912_nut_din562(l=10,d=3,nut_depth=4,screw_path=50,nut_path=30,fit=1.2,res=20);
        translate([40,rod_offset_y_b,5]) rotate(a=[0,90,0])screw_din912_nut_din562(l=10,d=3,nut_depth=4,screw_path=50,nut_path=30,fit=1.2,res=20);
    }
}
// translate([0,0,50]) rods_plate_single_bot(8,rod_diameter_tolerance);

module rods_plate_single_top(diameter,tolerance){
    difference(){
         hull(){
             //top plate
            for (i = [[-rod_offset_x_t+6,-rod_offset_y_t-2.75,0],[-rod_offset_x_t+6,rod_offset_y_t+2.75,0],[-rod_offset_x_t-36,-rod_offset_y_t+5,0],[-rod_offset_x_t-36,rod_offset_y_t-5,0],[-rod_offset_x_t-15,-rod_offset_y_t-2.75,0],[-rod_offset_x_t-15,rod_offset_y_t+2.75,0]]){
                translate([offset,0,rod_offset_z]) translate(i) cylinder(h=9,r=(diameter+4+tolerance)/2,center=false,$fn=res);
            }
            //bottom plate
            translate([0,0,-20]) for (i = [[-1,-1,0],[1,-1,0],[-1,1,0],[1,1,0]]){
                translate(i*(lens_mount_d_top/2-lens_mount_radius)) cylinder(h=1,r=lens_mount_radius,center=false,$fn=res);
            }
        }
        rods(diameter,rod_diameter_tolerance);
        //set screws

translate([10,-rod_offset_y_t,-4]) rotate(a=[0,-90,180]) rotate(a=[0,0,0]) screw_din912_nut_din562(l=12,d=4,nut_depth=4,screw_path=50,nut_path=30,fit=1.2,res=20);
translate([10,rod_offset_y_t,-4]) rotate(a=[0,-90,180])rotate(a=[0,0,0])screw_din912_nut_din562(l=12,d=4,nut_depth=4,screw_path=50,nut_path=30,fit=1.2,res=20);
//holes for MC mounting
translate([-15,-rod_offset_y_t-10,-4.5]) rotate(a=[0,90,-90]) rotate(a=[0,0,180]) screw_din912_nut_din562(l=16,d=3,nut_depth=10,screw_path=50,nut_path=30,fit=1.2,res=20);
translate([-15,rod_offset_y_t+10,-4.5]) rotate(a=[0,90,90]) rotate(a=[0,0,180]) screw_din912_nut_din562(l=16,d=3,nut_depth=10,screw_path=50,nut_path=30,fit=1.2,res=20);
    }
}



//translate([0,0,0]) rods_plate_single_top(8,rod_diameter_tolerance);

module rods_plate_single_top2(diameter,tolerance){
    difference(){
         hull(){
        for (i = [[-rod_offset_x_t+6,-rod_offset_y_t-3,0],[-rod_offset_x_t+6,rod_offset_y_t+3,0],[-rod_offset_x_t,-rod_offset_y_t-3,0],[-rod_offset_x_t,rod_offset_y_t+3,0]]){
                translate([offset,0,rod_offset_z]) translate(i) cylinder(h=12,r=(diameter+4+tolerance)/2,center=false,$fn=res);
            }
        }
        rods(diameter,rod_diameter_tolerance);
        //set screws

translate([5,-rod_offset_y_t-10,-4]) rotate(a=[0,90,-90]) rotate(a=[0,0,90]) screw_din912_nut_din562(l=16,d=3,nut_depth=8,screw_path=50,nut_path=30,fit=1.2,res=20);
translate([5,rod_offset_y_t+10,-4]) rotate(a=[0,90,90]) rotate(a=[0,0,-90]) screw_din912_nut_din562(l=16,d=3,nut_depth=8,screw_path=50,nut_path=30,fit=1.2,res=20);
        
    }
}

//translate([0,0,0]) rods_plate_single_top2(8,rod_diameter_tolerance);


//////////////////////////////////////////////////////////////////////////////
// aiming laser

// laser pointer
laser_diameter=12; // diameter of the main body 12mm nominal plus some space
laser_offset=offset-36; // offset from lens center
laser_beam=6; // diameter of the output optical beam
laser_height=38; // height of the laser as such
laser_rubber_d=19; // diameter of the mounting rubber
laser_rubber_t=5; // thickness of the rubber

module aiming_laser(){
	//aiming rubber
	//translate([0,0,laser_rubber_t/2])
	//cylinder(h=laser_rubber_t,r=laser_rubber_d/2,center=true,$fn=res);
	//laser
	translate([0,0,laser_height/2])
	cylinder(h=laser_height,r=laser_diameter/2,center=true,$fn=res);
    //output path
	translate([0,0,0])
	cylinder(h=50,r=3,center=true,$fn=res);
}

//translate([laser_offset,0,-5]) aiming_laser();
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

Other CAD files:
main_structure/koruza-v10-sfp_mount.stl
main_structure/koruza-v10-comb-ring_inner-lens_mount.stl
enclosure/U profile 100x35x5.STEP
main_structure/koruza-v10-sfp_mount_bracket.stl
enclosure/L profile 100x100x5.DXF
enclosure/L profile 100x100x5.SLDDRW
enclosure/L profile 100x100x5.SLDPRT
enclosure/L profile 100x100x5.STEP
enclosure/U profile 100x35x5.DXF
enclosure/U profile 100x35x5.SLDDRW
enclosure/U profile 100x35x5.SLDPRT
enclosure/bolt_HEX_ISO4017_DIN933_M10x160.SLDPRT
enclosure/bolt_eye_DIN444A_M10x45.SLDPRT
enclosure/bolt_round_head_square_neck_DIN603_M10x70.SLDPRT
enclosure/enclosure.SLDDRW
enclosure/enclosure_cover.stl
enclosure/koruza enclosure.SLDDRW
enclosure/nut_DIN934_M4.SLDPRT
enclosure/nut_thin_ISO4035_M10.SLDPRT
enclosure/screw_HEX_SOCKET_ISO4762_DIN912_M4x12.SLDPRT
enclosure/square tube 100x100x2.SLDDRW
enclosure/square tube 100x100x2.SLDPRT
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

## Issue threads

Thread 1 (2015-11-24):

Laser mount screws too short

SloMusti, 2015-11-24:
The nuts is part [Laser mount](https://github.com/IRNAS/KORUZA/blob/master/main_structure/koruza-v10-laser_mount.stl) are positioned too hig and thus the 35mm long screws are a bit to short.

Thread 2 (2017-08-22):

incomplete Gerber files

stkdiretto, 2017-08-22:
All gerber folders save the RPI shield one are missing the respective GKO file, which make panelizing the boards impossible for me (using gerbertools).

I'd export the gerbers anew, but alas, the sources are Altium and not KiCAD, so I can't :(

SloMusti, 2017-08-23:
Layer GM3 contains the outline you require, simply rename it to GKO and it shall serve your purpose.

Also: See KORUZA Pro electronics if that may server your purpose better. https://github.com/IRNAS/KORUZA-Pro

stkdiretto, 2017-09-07:
Thank you, this solved the problem

Closed 2017-09-07.

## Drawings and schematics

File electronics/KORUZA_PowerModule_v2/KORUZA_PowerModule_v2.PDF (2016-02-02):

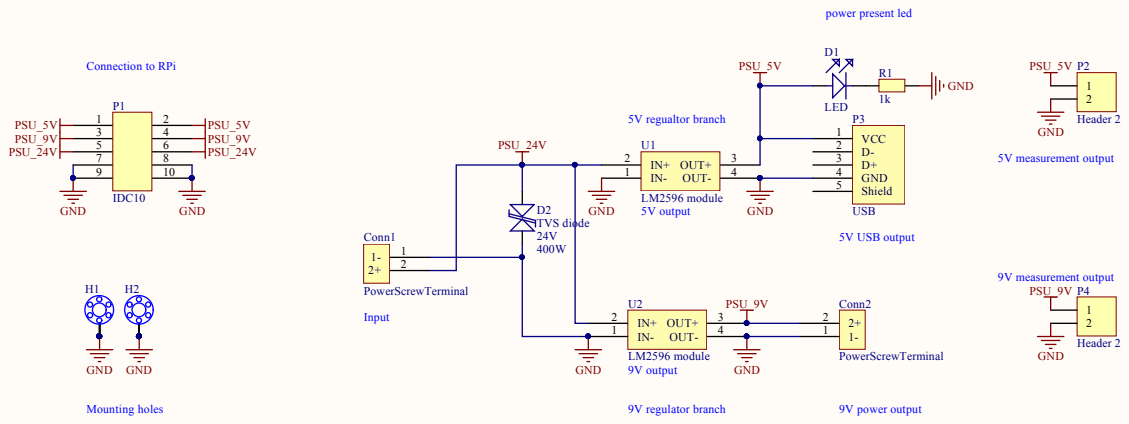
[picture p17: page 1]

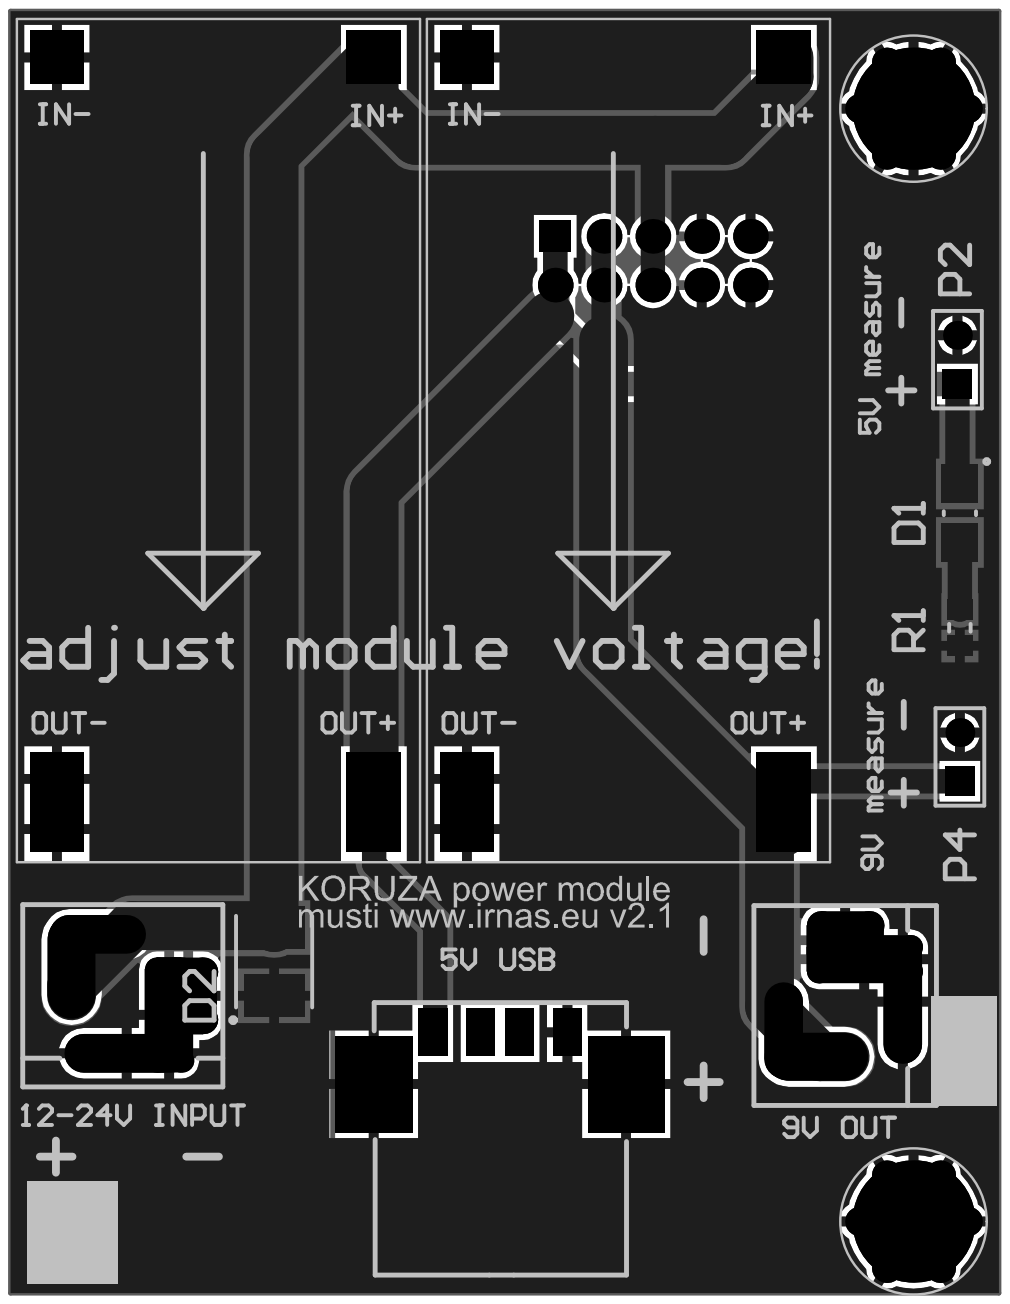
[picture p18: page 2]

Comment | Description | Designator | Footprint | LibRef | Quantity
PowerScrewTerminal | | Conn1, Conn2 | MKDSN 2,5/ 2-5,08 | PowerScrewTerminal | 2
LED | LED diode | D1 | 1206/0805 diode | LED | 1
TVS diode | TVS bidirectional diode | D2 | DIOM4750X18N | TVS diode | 1
IDC10 | IDC 10pin | P1 | IDC10 | IDC10 | 1
Header 2 | Header, 2-Pin | P2, P4 | HDR1X2 | Header 2 | 2
USB | USB A standard receptacle | P3 | USB A THT | USB | 1
1k | Resistor 0805 smd | R1 | RESC2012X06N | Resistor | 1
LM2596 module | LM2596 module | U1, U2 | LM2596 module | LM2596 module | 2

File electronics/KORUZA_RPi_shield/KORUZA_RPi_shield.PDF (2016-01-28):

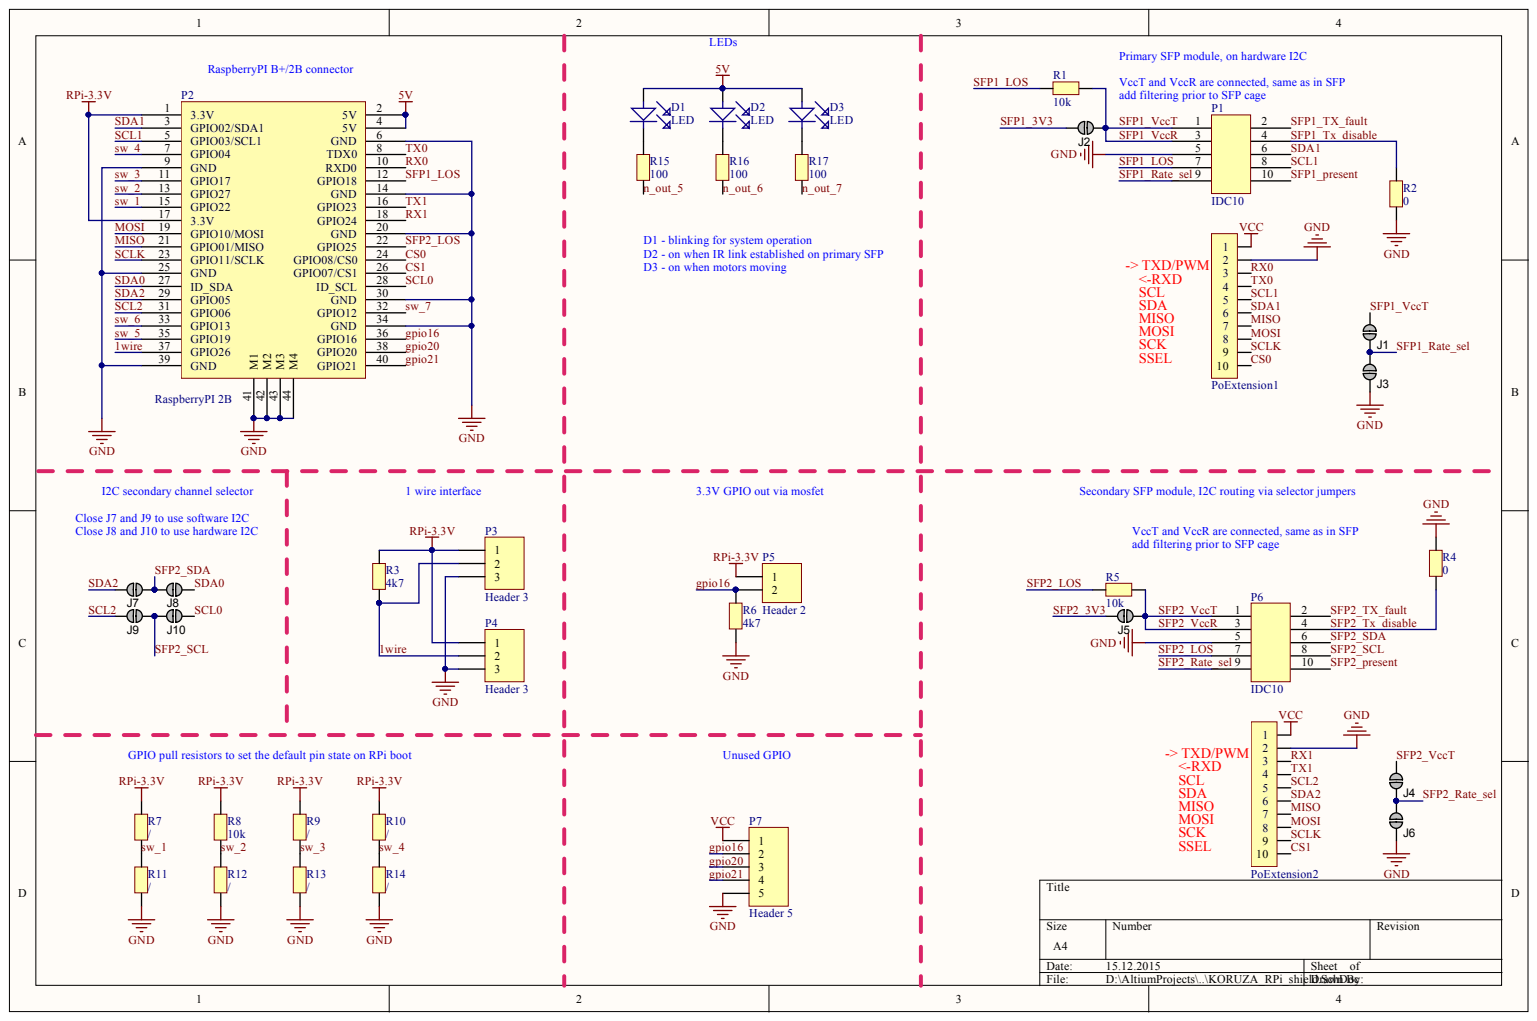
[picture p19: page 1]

-> TXD/PWM <-RXD SCL SDA MISO MOSI SCK SSEL

ielDd.Sch rawnD Byoc

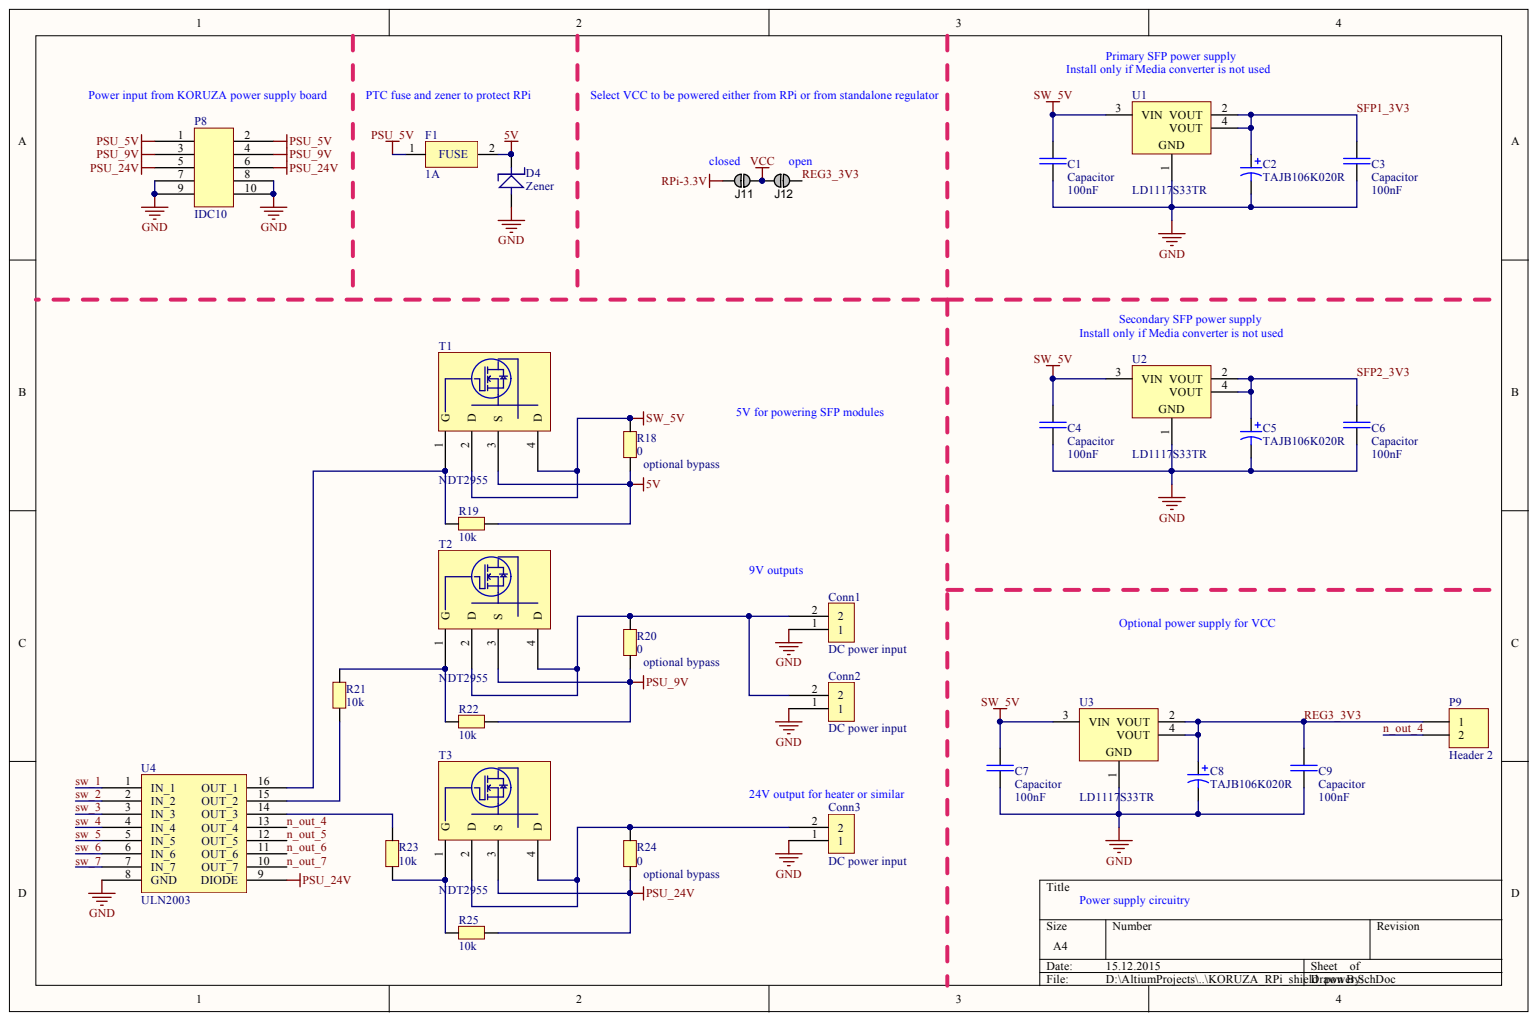
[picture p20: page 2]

Primary SFP power supply

Install only if Media converter is not used

Secondary SFP power supply

5V for powering SFP modules

Optional power supply for VCC

24V output for heater or similar

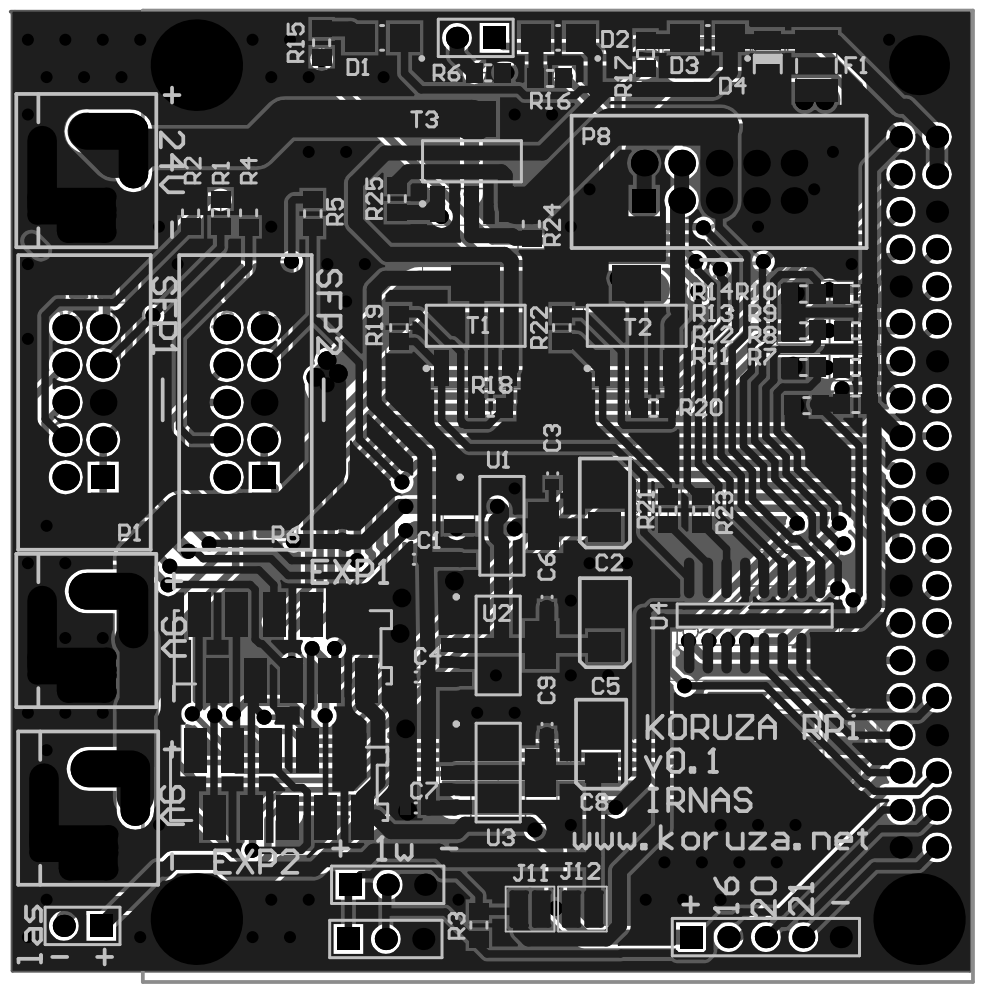
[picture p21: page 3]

Comment | Description | Designator | Footprint | LibRef | Quantity
Capacitor | General capacitor | C1, C3, C4, C6, C7, C9 | 0603 | Capacitor | 6
TAJB106K020R | Capacitor, Tantalum, 10uF 10% 20V MCCT-B (3528) | C2, C5, C8 | AVX-CAPC3528_V | CMP-0279-00001-1 | 3
DC power input | | Conn1, Conn2, Conn3 | MKDSN 2,5/ 2-5,08 and powercon | PowerScrewTerminal | 3
LED | LED diode | D1, D2, D3 | 1206/0805 diode | LED | 3
Zener | Zener | D4 | DIOMELF3517N | Zener | 1
1A | 1A fuse | F1 | 1210 | Fuse | 1
IDC10 | IDC 10pin | P1, P6, P8 | IDC10 | IDC10 | 3
RaspberryPI 2B | RPi2 | P2 | RaspberryPI_B+ | RaspberryPI 2B | 1
Header 3 | Header, 3-Pin | P3, P4 | HDR1X3 | Header 3 | 2
Header 2 | Header, 2-Pin | P5, P9 | HDR1X2 | Header 2 | 2
Header 5 | Header, 5-Pin | P7 | HDR1X5 | Header 5 | 1
| Micro-Match female PCB connector 10 Positions THT | PoExtension1, PoExtension2 | 8-188275-0 | 1-215079-0 | 2
10k | Resistor 0805 smd | R1, R5, R8, R19, R21, R22, R23, R25 | RESC2012X06N | Resistor | 8
0 | Resistor 0805 smd | R2, R4, R18, R20, R24 | RESC2012X06N | Resistor | 5
4k7 | Resistor 0805 smd | R3, R6 | RESC2012X06N | Resistor | 2
/ | Resistor 0805 smd | R7, R9, R10, R11, R12, R13, R14 | RESC2012X06N | Resistor | 7
100 | Resistor 0805 smd | R15, R16, R17 | RESC2012X06N | Resistor | 3
NDT2955 | P MOSFET | T1, T2, T3 | SOT230P700X180-4N | NDT2955 | 3
LD1117S33TR | Fixed Low Drop Positive Voltage Regulator, 3.3V, 4-Pin SOT-223, Tape and Reel | U1, U2, U3 | SOT-223_L | CMP-0244-00310-1 | 3
ULN2003 | Darlington array | U4 | SO-16 narrow | ULN2003 | 1

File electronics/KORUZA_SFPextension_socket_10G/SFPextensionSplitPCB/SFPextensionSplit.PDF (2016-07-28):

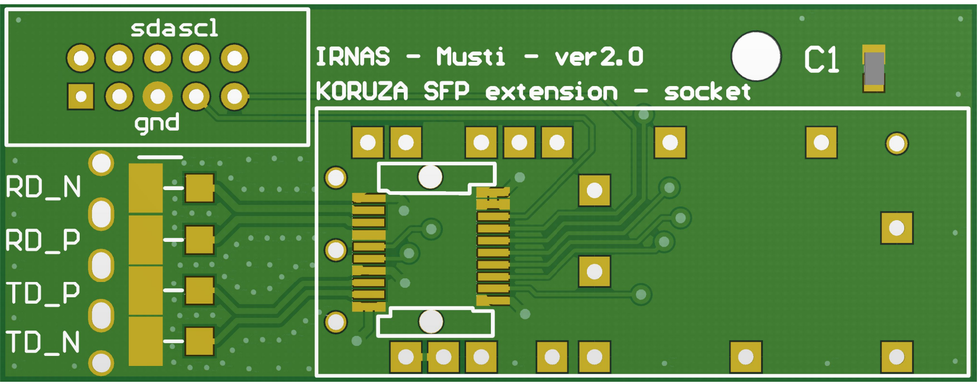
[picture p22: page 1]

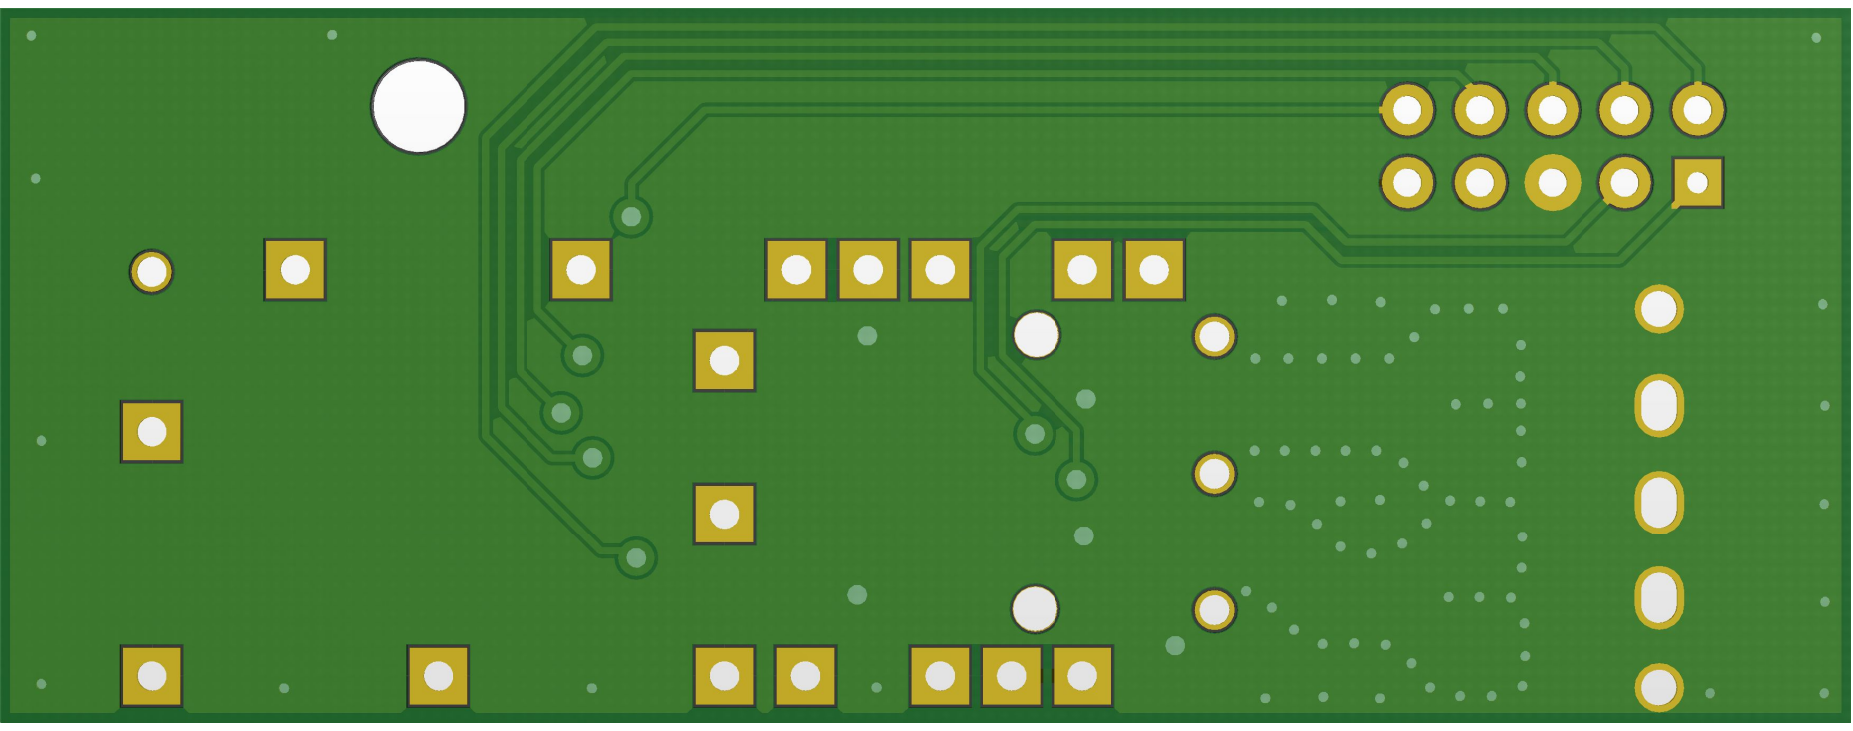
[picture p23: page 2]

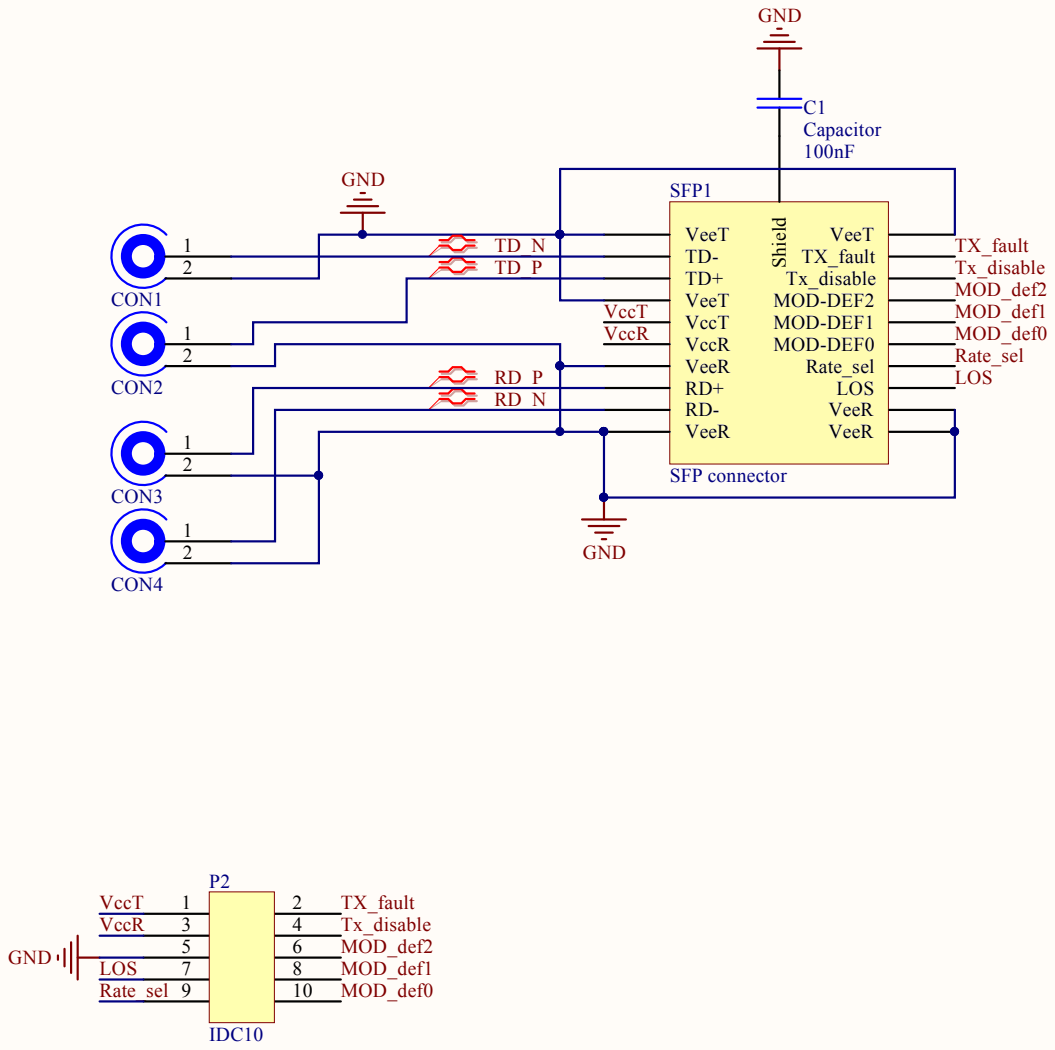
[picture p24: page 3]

TD-TX_fault TD+ Tx_disable VeeT MOD-DEF2 VccT MOD-DEF1 VccR MOD-DEF0 VeeR Rate_sel RD+ LOS RD-VeeR

VeeR

Title
Musti - Institute IRNAS Rače www.irnas.eu
License: CC BY-NC-SA 3.0

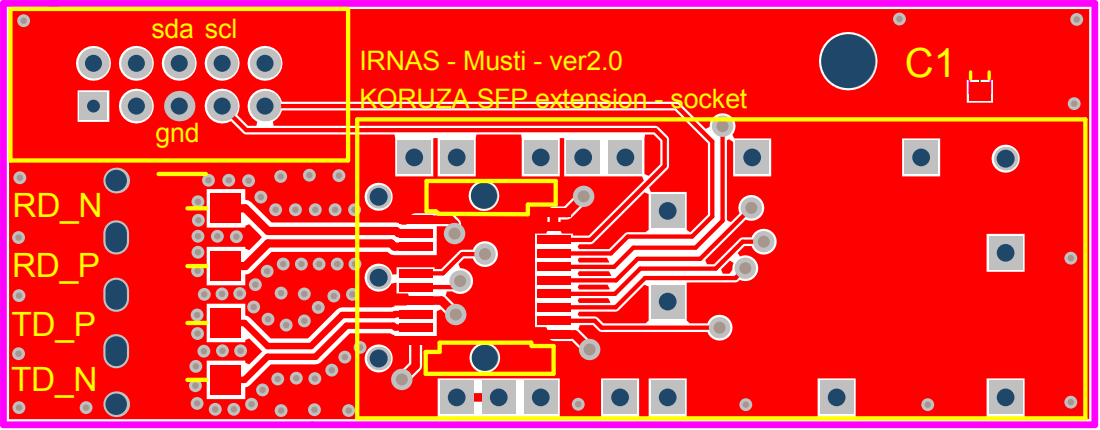
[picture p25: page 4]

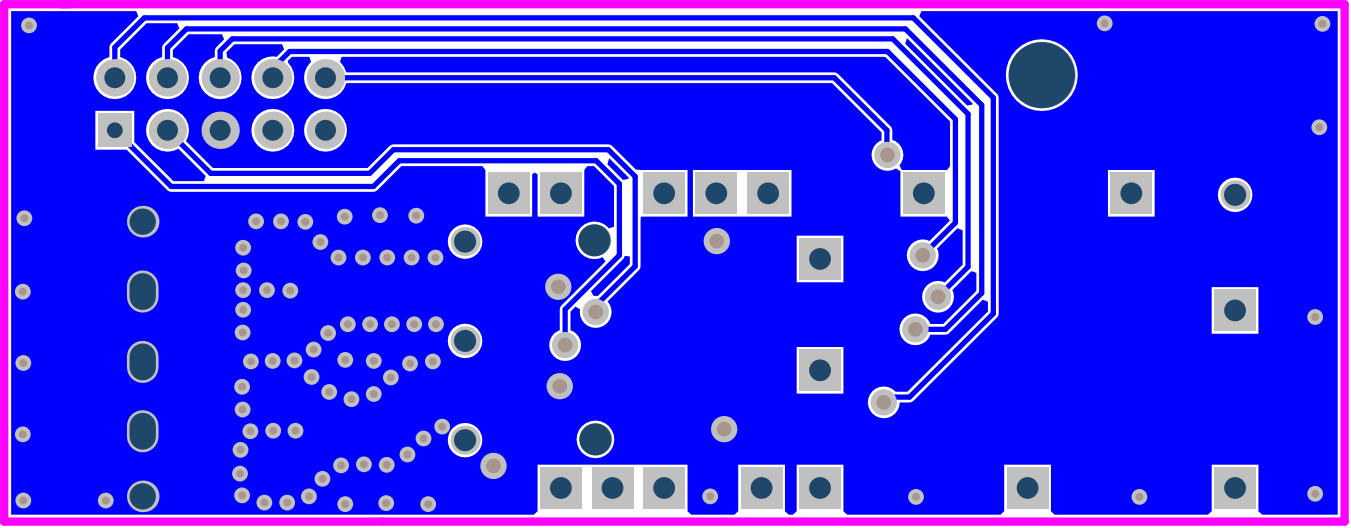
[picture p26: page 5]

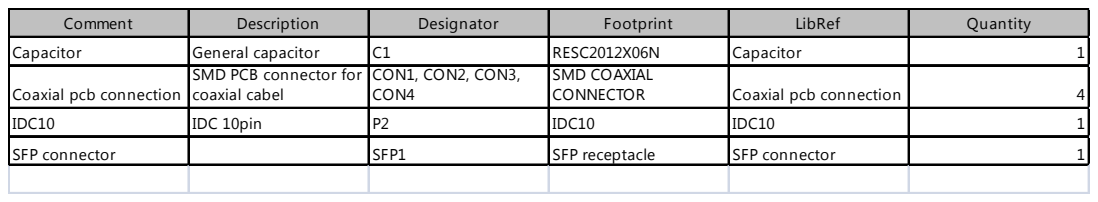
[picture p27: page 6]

Comment | Description | Designator | Footprint | LibRef | Quantity

Capacitor | General capacitor | C1 | RESC2012X06N | Capacitor | 1
Coaxial pcb connection | SMD PCB connector for coaxial cabel | CON1, CON2, CON3, CON4 | SMD COAXIAL CONNECTOR | Coaxial pcb connection | 4

IDC10 | IDC 10pin | P2 | IDC10 | IDC10 | 1

SFP connector | | SFP1 | SFP receptacle | SFP connector | 1

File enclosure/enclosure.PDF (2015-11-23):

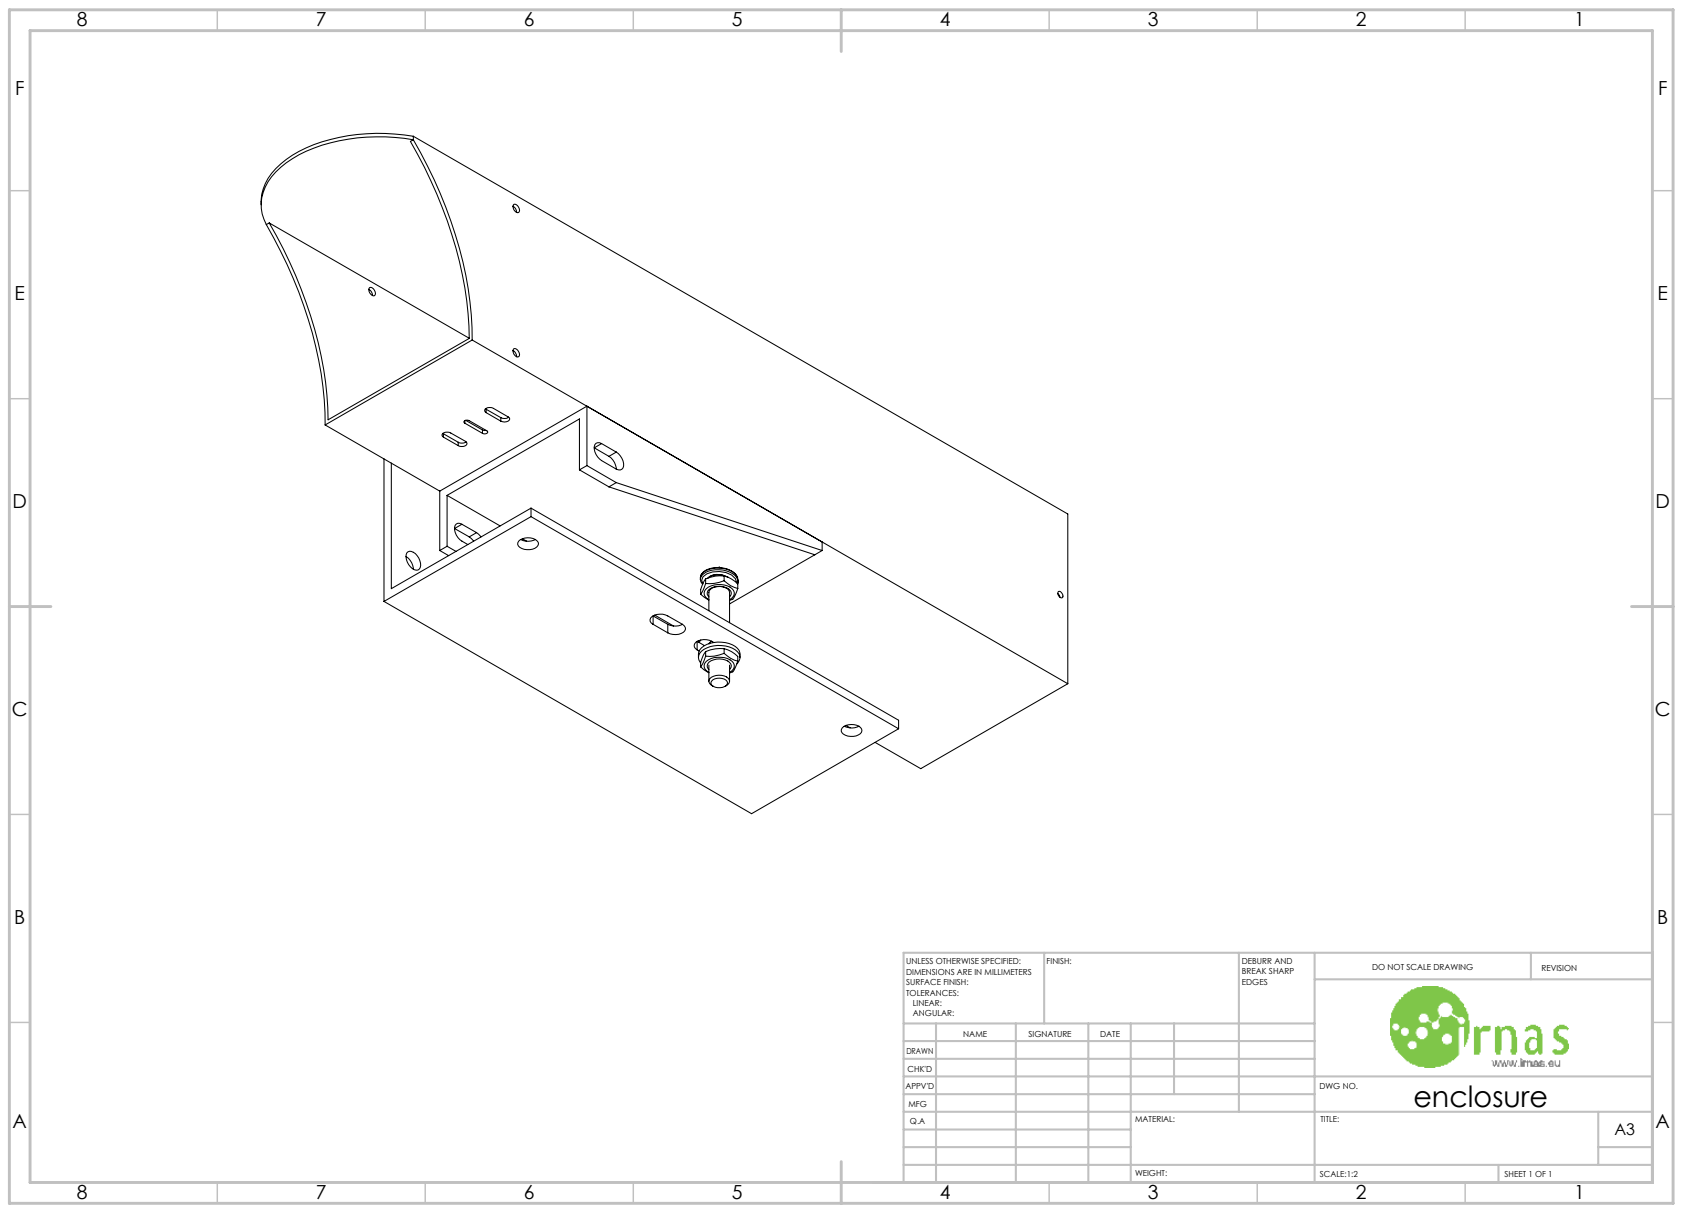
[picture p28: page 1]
FINISH:; DEBURR AND; BREAK SHARP; DO NOT SCALE DRAWING; REVISION; SCALE:1:2; SHEET 1 OF 1

UNLESS OTHERWISE SPECIFIED:
DIMENSIONS ARE IN MILLIMETERS
SURFACE FINISH:
TOLERANCES:
LINEAR:
ANGULAR:

NAME | SIGNATURE | DATE

DRAWN
CHK'D
APPV'D | | | | | | | enclosure DWG NO.

MFG
Q.A | | | | MATERIAL: | TITLE: | A3

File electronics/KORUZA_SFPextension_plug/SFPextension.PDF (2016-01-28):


VeeR
VeeT TD- TD+ VeeT VccT VccR VeeR


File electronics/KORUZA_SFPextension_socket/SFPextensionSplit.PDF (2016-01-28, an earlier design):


Title
Musti - Institute IRNAS Rače www.irnas.eu
License: CC BY-NC-SA 3.0



Comment | Description | Designator | Footprint | LibRef | Quantity

Capacitor | General capacitor | C1 | RESC2012X06N | Capacitor | 1

SATA | sata | P1 | SATA pcb | SATA | 1

IDC10 | IDC 10pin | P2, P3 | IDC10 | IDC10 | 2

SFP connector | | SFP1 | SFP receptacle | SFP connector | 1

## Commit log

2015-01-06 Enclosure design
    [Enclosure.dwg, Enclosure.stp]
2015-01-06 Mounting details
2015-01-22 Adding the 3D printable lid / back cover.
    OpenSCAD design in use with generation 5.
    [koruza-lid.scad, koruza-lid.stl]
2015-04-14 Adding files
    [koruza-v5-A0-lid.stl, koruza-v5-A1-main-shorter.stl, koruza-v5-A2-arm.stl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]
2015-07-21 Introducing new generation
    [koruza-v10-filegen.scad, koruza-v10-ring_and_lens_mount_outer.stl, koruza-v10.scad]
2015-07-21 additional changes
    [koruza-v5-A0-lid.stl, koruza-v5-A1-main-shorter.stl, koruza-v5-A2-arm.stl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]
2015-07-22 Adding another piece
    [koruza-v10-filegen.scad, koruza-v10-ring_inner_and_laser_mount.stl]
2015-07-26 Beta configuration for verification
    [koruza-v10-comb-ring_inner-lens_mount.stl, koruza-v10-comb-ring_outer-lens_outer.stl, koruza-v10-filegen.scad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]
2015-08-12 koruza 1.0 parts update
    [koruza-v10-comb-ring_inner-lens_mount.stl, koruza-v10-comb-ring_outer-lens_outer.stl, koruza-v10-filegen.scad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]
2015-08-28 Modifications for reliable assembly,
    [koruza-v10-comb-ring_inner-lens_mount.stl, koruza-v10-comb-ring_outer-lens_outer.stl, koruza-v10-filegen.scad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]
2015-09-04 Added a recess for SFP board attachment screw head
    [koruza-v10-sfp_mount.stl, koruza-v10.scad]
2015-09-07 adding missing parts
    couplers, sleeve for electronics sfp insert, alu bracket
    [koruza-v10-coupler.stl, koruza-v10-couplerM4.stl, koruza-v10-sfp_alu_bracket.stl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]
2015-09-28 Update on 1.0 parts, enclosure added
    [Enclosure.dwg, Enclosure.stp, L profile 100x100x5.DXF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]
2015-11-15 Rubber set rings and spring mounting hole
    [koruza-v10-comb-ring_inner-lens_mount.stl, koruza-v10-comb-ring_outer-lens_outer.stl, koruza-v10-filegen.scad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]
2015-11-17 fixed bug with motor mount
    [koruza-v10-motor_mount.stl, koruza-v10.scad]
2015-11-23 Enclosure adjustment holes extension
    [L profile 100x100x5.SLDPRT, U profile 100x35x5.SLDPRT, bolt_HEX_ISO4017_DIN933_M10x160.SLDPRT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]
2015-11-24 Laser mount screws slots moved and comments added
    [koruza-v10-laser_mount.stl, koruza-v10.scad]
2015-12-01 Changed focus adjustment motorized setup
    Solved the problem of inconsistent movement on F axis.
    [koruza-v10-comb-ring_inner-lens_mount.stl, koruza-v10-comb-ring_outer-lens_outer.stl, koruza-v10-filegen.scad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]
2015-12-02 Adding missing files and removing unused ones
    [koruza-v10-couplerM4.stl, koruza-v10-enclosure_cover_long.stl, koruza-v10-pin-hole.stl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]
2015-12-02 Initial comit of BoM
    [koruza-v10-BillOfMaterials.ods]
2015-12-03 Fixing misconfigured aprts
    [koruza-v10-laser_mount.stl, koruza-v10-motor_mount.stl, koruza-v10-rpi_plate.stl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]
2015-12-03 removing unused part
    [koruza-v10-rpi_plate.stl]
2015-12-03 Missing 3D printed parts
    [koruza-v10-halfbracket.stl, koruza-v10-triangle.stl]
2015-12-04 minor BoM corrections
    [koruza-v10-BillOfMaterials.ods]
2016-01-28 electronics update
    [KORUZA_PowerModule_v2.GBL, KORUZA_PowerModule_v2.GBO, KORUZA_PowerModule_v2.GBP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]
2016-02-02 Added spreadsheets will bills of materials
    [KORUZA_PowerModule_v2-BillOfMaterials.xls, KORUZA_RPi_shield-BillOfMaterials.xls, SFPextension-BillOfMaterials.xls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]
2016-07-28 SFP extension socket 10G add
    [PCB_connectors.SchLib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]
2016-08-16 Added parts for 10G version.
    [KORUZA_RPi_shield-BillOfMaterials.xls, koruza-v10-10G-enclosure-cover-lid.stl, koruza-v10-10G-enclosure-cover.stl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]
